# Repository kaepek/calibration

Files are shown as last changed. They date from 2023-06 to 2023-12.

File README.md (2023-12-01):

# KAEPEK-CALIBRATION V1.3.0

A calibration library for synchronising bldc motor voltage models with digital absolute position rotary encoders. Note for now this library is only configured for using the AS5147P encoder with [this breakout circuit](https://www.mouser.co.uk/ProductDetail/ams-OSRAM/AS5147P-TS_EK_AB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)

# Galvanically isolated ADC/Encoder circuit
[Circuit](./circuits/calibration/circuit)

## Connecting AS5147P breakout circuit to the calibration circuit

Connection is made by simply connecting a 8 pin header ribbon cable between the encoder and the calibration circuit. See below:

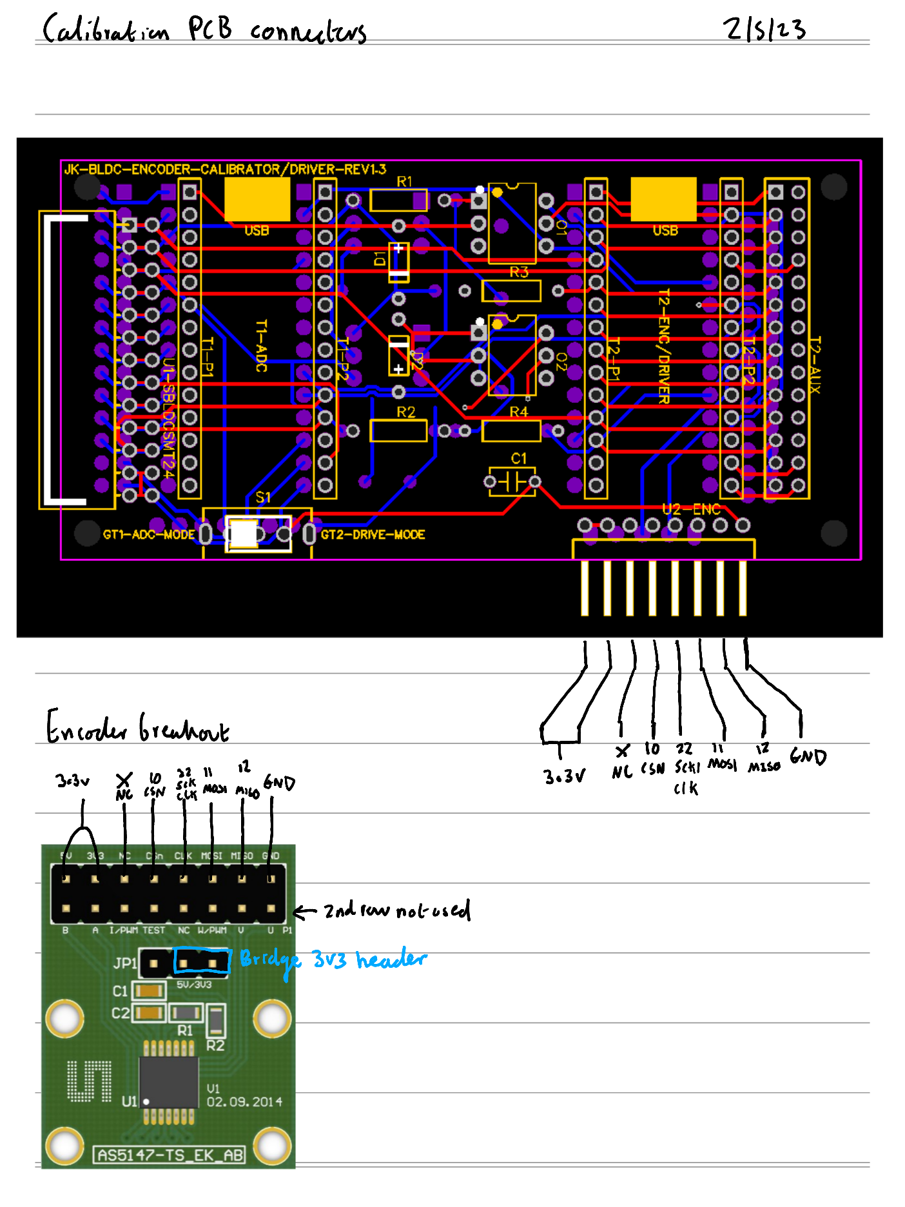
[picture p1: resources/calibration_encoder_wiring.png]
calibration connections


# KAEPEK-SBDLC-SMT-V2.4.0 circuit

[Circuit](https://github.com/kaepek/sbldc-smt/tree/e0ab160f8fc606f709ad24c7c99f17e19a991b6a/circuit)

## Connecting KAEPEK-SBDLC-SMT-V2.4.0 circuit to the calibration circuit

Connection is made by simply connecting the 13 pin header from the KAEPEK-SBDLC-SMT-V2.4.0 pcb to the KAEPEK-Calibration circuit pcb with the surface mount components point upwards. 

# Collecting ADC Encoder data for calibration instructions

## Prerequisites to collection procedure

Need two computers to collect clean data from this setup. The computer must remain isolated from each other not sharing a ground connection (both cannot have ethernet connecting to the same device, stick to WiFi).

- Install node.js (v18.12.1) and npm (8.19.2) have been checked to work.
- Run `npm install` in the projects root directory.
- Install [`kaepek-io`](https://github.com/kaepek/io) as per the README instructions.

## Collection procedure

1. Modify zero_crossing_adc.ino and set the PWM_FREQUENCY to full calibration logging speed e.g. 90kHz.
2. Make sure zero_crossing_adc.ino has been loaded onto the Teensy 4.0 #1.
3. Make sure AS5147P_teensy40.ino has been loaded onto the Teensy 4.0 #2.
4. Find network address of computer #1 and computer #2 by running `ifconfig` or similar. e.g. '192.168.0.15'.
5. Plug Teensy 4.0 #2 (Encoder) into computer #2.
6. Plug Teensy 4.0 #1 (ADC) into computer #1
7. Unplug and replug Teensy 4.0 #1 into computer #1 (forcing a reset).
8. Start the network sync program on computer #1 and provide a name for this data collection run e.g. 'aug_18_test_1'. `npm run network-serial:collect-sync --run_id=aug_18_test_1`. 
9. SSH to computer #2.
10. Start the network source program on computer #2. `npm run network-serial:collect-source --device_id=1 --sync_host=10.0.0.110 --seconds_to_collect=2` .
11. Use a power drill to spin the motor at a constant high angular velocity.
12. Start the network source program on computer #1. `npm run network-serial:collect-source --device_id=0 --sync_host=0.0.0.0 --seconds_to_collect=2` .
13. After you are happy enough data has been collected stop collection by unplugging Teensy 4.0 #1.
14. Ensure `network-serial:collect-source` is stopped for both computers. By typing `Ctrl-c` into the relevant terminal sessions.
15. At this point the `network-serial:collect-sync` will merge the dataset and create an output file `./calibration-data/[run_id].jsonl` on computer #1. If this does not work try manually merging the files, see the next section below, otherwise move on to [data analysis section](#data-analysis).

# Data analysis

Depending on what type of motor controller you are implementing there are different analysis commands you need to run.
The calibration library provides for 3 main types of motor controller:

- 6 step, 3 phase H-Bridge, PWM motor controllers (Trapezoidal Commutation [TC])
- 3 phase H-Bridge, sinusoidal fit (Sinudoidal model fit fom BEMF measurements) PWM motor controllers (Sinusoidal PWM [SPWM])
- 3 phase H-Bridge, direct fit (fit direcly from BEMF measurements) PWM motor controllers (Direct PWM [DPWM])

In either case the raw capture data needs to be combined from the ADC and Encoder microcontroller collected data (for each run) and the result processed to smooth out errors via the [combination and smoothing procedure](#combination-and-smoothing-procedure)

## Prerequisites to performing any Data analysis

- Create a virtual environment: `npm run install:venv`
- Source the virtual environment (must be active before running analysis or for each new terminal session): `source env/bin/activate`
- Install the virtual environment dependancies: `npm run install:venv-deps`

## Combination and smoothing procedure

0. Requires that data has been collected following the [data collection procedure](#collection-procedure)
1. One can run the combination and smoothing process with existing settings (determined by trial and error) using the following command (make sure to check the `kalman_smoothed_merged_capture_data.html` and the `zero_crossing_detections.channels.inliers.html` file! This step is not easily automatable):
  - `npm run combine-and-smooth:rotation-voltage-data -run_id=[run_id]`

Examples of good captures:
  - [Good ADC / Encoder capture with Kalman filtering example output of smooth:rotation-voltage-data for a motor with approximately a sinusoidal bemf motor (A2212)](./dist/kalman_smoothed_merged_capture_data.html)
  - [Good ADC / Encoder with a Kalman filtered example output of smooth:rotation-voltage-data for a motor with a trapazodial bemf motor (Tarot 4006)](./dist/kalman_smoothed_merged_capture_data_tarot4006_sept_12_23_cw_3_trapazodial.html)

Examples of bad captures:
  - [Bad capture example 1- High noise](./dist/kalman_smoothed_merged_capture_data_a2212_jul_26_2s_cw_1_high_noise.html)
  - [Bad capture example 2 - One channel higher](./dist/kalman_smoothed_merged_capture_data_a2212_oct_21_cw_1_higher_channel.html)
  - [Sync loss with one channel also higher](./dist/kalman_smoothed_merged_capture_data_a2212_oct_21_ccw_1_sync_loss.html)
  - [Dead channel](./dist/kalman_smoothed_merged_capture_data_a2212_mar_14_2s_cw_dead_channel.html)

## Fitting procedures:

Then depending on which motor controller you are implementing (TC, SPWM, DPWM) you need to follow the relevant section:

### TC procedure

The TC procdure will map angular segments of the motor to their commutation state. Such that microcontrollers can simply lookup the commutation state based on the angle that the encoder currently sits and therefore apply the correct commutation state as the motor proceeds around the circle. A map is generated for each direction.

The TC procedure require Apache Spark installation v3.5.0 and Spark must be running locally by running the relevant start script e.g. `./spark-3.5.0-bin-hadoop3/sbin/start-all.sh`. Configure the `package.json` spark master url etc.

0. Run the [combination and smoothing procedure](#combination-and-smoothing-procedure)
1. Perform the TC analysis: `npm run perform-tc-analysis --run_id=[run_id] --number_of_poles=[number of poles]`

Then after inspecting the analysis for each run and determining a set of `run_id`s which represent good captures (no artifacts) one can then combine the multiple runs together and obtain the analysis reports and resulting fits for the TC procedure:

2. `npm run combine-datasets:zero-crossing-inliers --run_ids=16sept_ccw,16sept_4_cw`

A html file e.g. `combination-report-lqwkwldkjpvgmrbeqcop.html`, an id file e.g.
`combination-report-lqwkwldkjpvgmrbeqcop.id` and a 6 step fit c++ file `commutation_state_lqwkwldkjpvgmrbeqcop.cpp` will be created in the [calibration-data folder](./calibration-data/), `lqwkwldkjpvgmrbeqcop` represents the identifier for the combined set of analysed run results. Make sure to check for artifacts from the combined report and remove any run_ids where there is bad data.

### SPWM procedure

The SPWM procedure will take the results from the TC/Smoothing procedure and do its best to fit 3 sinusoids to the data (for each phase), for each direction an angular displacement (degrees away from the 0th encoder step) and an angular phase displacement (the phase seperation between the 3 phases) which leads to the least squares error. Thus the motor constants can be used to create a lookup table within the motor controller so that for each direction the controller can apply an appropriate duty for each phase give an input which is the encoder step at any given time.

1. Peform the same instructions as the [TC procedure section](#tc-procedure)
2. Fit a sinusoid model to the data using either of the following commands:
    - Fit a sine wave to the zero crossing data obtained from the TC procedure: `npm run fit-sine:zc --combination_identifier=lqwkwldkjpvgmrbeqcop --number_of_poles=22`
    - Fit a sine wave to the raw zero crossing data obtained from the TC procedure: `npm run fit-sine:raw --combination_identifier=lqwkwldkjpvgmrbeqcop --number_of_poles=22`

Note the `fit-sine:zc` benefits from significant outlier reduction and so in most cases represents the superior method to obtaining the motor constant fits. Depending on the sinusoidal fit method run one can either obtains the motor constants from the following files in the [calibration folder](./calibration-data/), `zc_reconstruction_lqwkwldkjpvgmrbeqcop.png` which is the output of running the `fit-sine:zc` program or `raw_reconstruction_ynitlldoqesyyvgyuwyg.png` which is the ouput of running the `fit-sine:raw` program.

### DPWM procedure

To deal with the inadequacies of the SPWM fitting method arising from the fact that no motors are in fact manufactured perfectly (discrepancies in motor pole strength and inperfect pole spacing) the direct bemf fit method is implemented here. This precedure takes the raw combination data (bemf voltage and angle data) for each run and then superimposes the data (grouped by the encoder angle) and then averages the for each angle the voltage, it applies a normalisation per channel such that one can obtain a single lookup table per direction per phase which informs the motor controller what duty to apply given an input encoder step at any given time. The normalised data can then be loaded into a relevant microcontroller and used the model used to drive the motor forward in a given direction.

This procedure offer the most efficient motor controller model fit of any of the methods proposed here, as the motor phase voltages are played back from direct recordings of the bemf and thus track them quite accurately.

0. Run the [combination and smoothing procedure](#combination-and-smoothing-procedure)
1. Run a direct fit:
    - If you have already run a TC procedure prior to this analysis you may run the following example command: `npm run fit-direct:raw --combination_identifier=lqwkwldkjpvgmrbeqcop`
    - Otherwise you can directly obtain a fit using the following example command: `npm run fit-direct-solo:raw --run_ids=16sept_ccw,16sept_4_cw && npm run graph-direct-solo:raw`, you will obtain an output html, png and c++ file e.g. `combination-direct-fit-ewgtelyqvgfuvropsmif.csv.html`, `raw_reconstruction_direct_comp2_ewgtelyqvgfuvropsmif.png`, `combination-direct-fit-ewgtelyqvgfuvropsmif.cpp`

# Troubleshooting:

- Permission denied when trying to run `network-serial:collect-source`
  - Change permissions for Teensy device `sudo chmod a+rw /dev/ttyACM0`
- One voltage channel 's(A,B,C) peak (in inspect) is larger than the other one.
  - Check circuit connections

# Documentation
Requires running `npm run generate:docs`

- [JS Docs](./docs/global.html)
- Python Docs (TODO)

# 3rd party useful component information:

## H11L1 Opto-isolator

- [Datasheet](https://www.mouser.com/datasheet/2/149/H11L1M-1010369.pdf)

## AS5147P Encoder

- [Datasheet](https://ams.com/documents/20143/36005/AS5147P_DS000328_2-00.pdf)

# How to prepare the Teensy40 platform:
- Install [Arduino IDE v1.8.19](https://www.arduino.cc/en/software)
- Install [Teensyduino v2.1.0](https://www.pjrc.com/teensy/teensyduino.html)

# General dependancies:

- [Arduino.h](https://github.com/arduino/ArduinoCore-avr)
- [imxrt.h](https://github.com/PaulStoffregen/cores/tree/master)
- [Serialport](https://github.com/serialport/node-serialport/blob/main/LICENSE)
- [Bokeh](https://github.com/bokeh/bokeh/blob/branch-3.4/LICENSE.txt)
- [Typed struct](https://github.com/sarakusha/typed-struct/blob/main/LICENSE)
- [Extensionless](https://github.com/barhun/extensionless/blob/main/LICENSE)
- [Cross var](https://github.com/elijahmanor/cross-var/blob/master/LICENSE)
- [JS promise socket](https://github.com/dex4er/js-promise-socket)
- [JS Doc](https://github.com/jsdoc/jsdoc/blob/main/LICENSE)
- [Numpy](https://github.com/numpy/numpy/blob/main/LICENSE.txt)
- [Pandas](https://github.com/pandas-dev/pandas)
- [Spark](https://github.com/apache/spark/blob/master/LICENSE)
- [netifaces](https://alastairs-place.net/projects/netifaces/)
- [pyarrow](https://github.com/apache/arrow/blob/main/LICENSE.txt)
- [scipy](https://github.com/scipy/scipy)
- [colour](https://github.com/vaab/colour/blob/master/LICENSE)
- [matplotlib](https://github.com/matplotlib/matplotlib)

## [See the long version of this article](./README-LONG.md)

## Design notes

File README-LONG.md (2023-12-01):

# KAEPEK-CALIBRATION V1.3.0

A calibration library for synchronising bldc motor voltage models with digital absolute position rotary encoders. Note for now this library is only configured for using the AS5147P encoder with [this breakout circuit](https://www.mouser.co.uk/ProductDetail/ams-OSRAM/AS5147P-TS_EK_AB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)

# Quickstart Guide

Recommended [read the quick start guide here](./README.md).
For more comprehensive instructions continue below.

# Galvanically isolated ADC/Encoder circuit

[Circuit](./circuits/calibration/circuit)

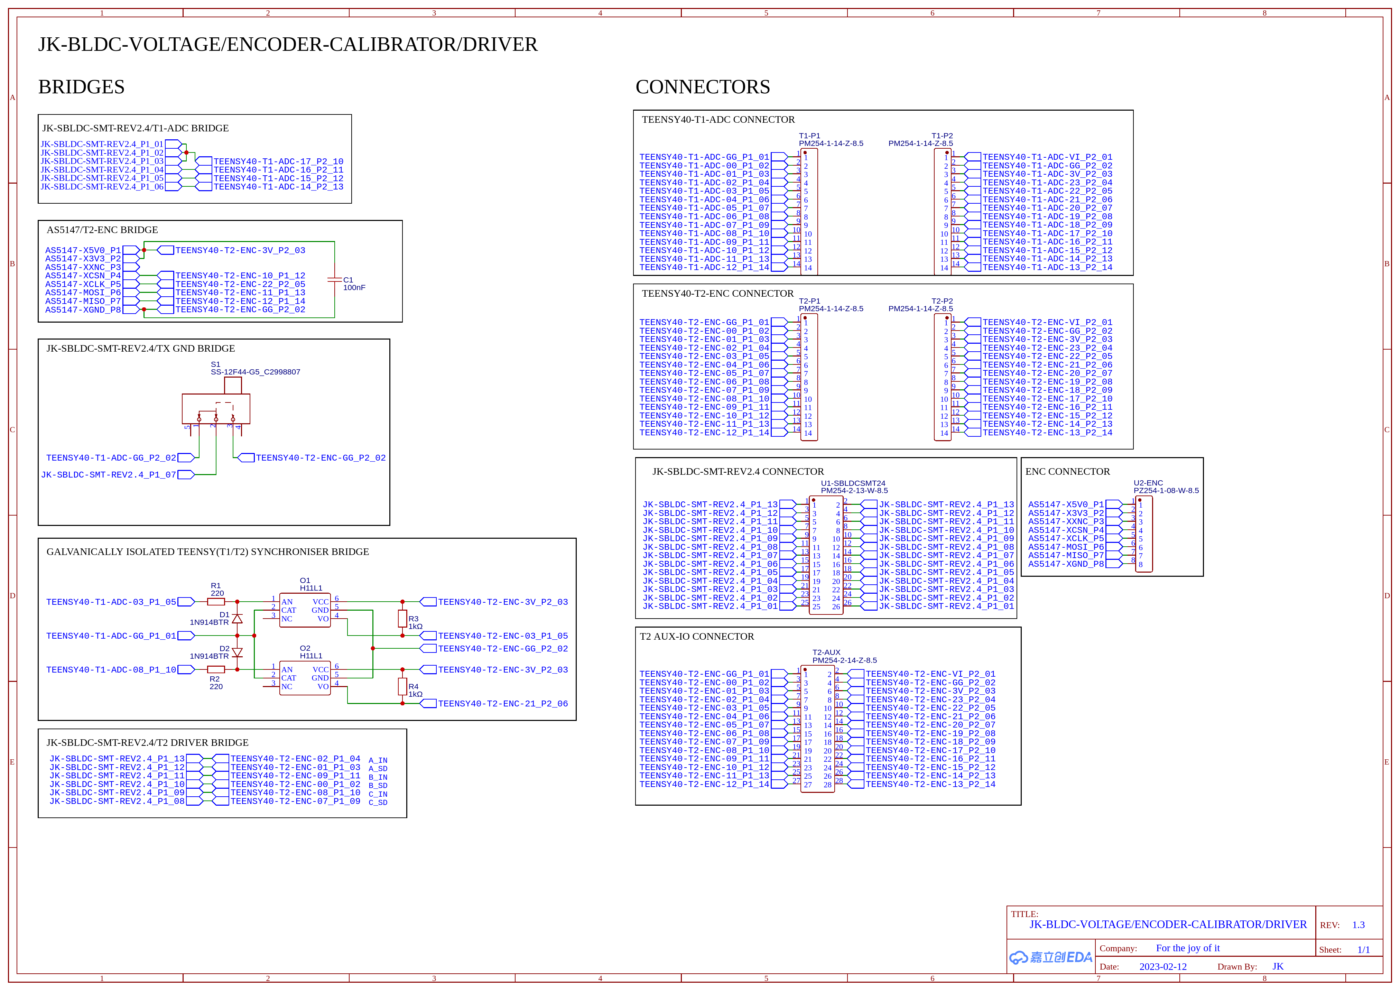
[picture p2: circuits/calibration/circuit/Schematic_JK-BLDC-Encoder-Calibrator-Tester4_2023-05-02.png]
calibration circuit


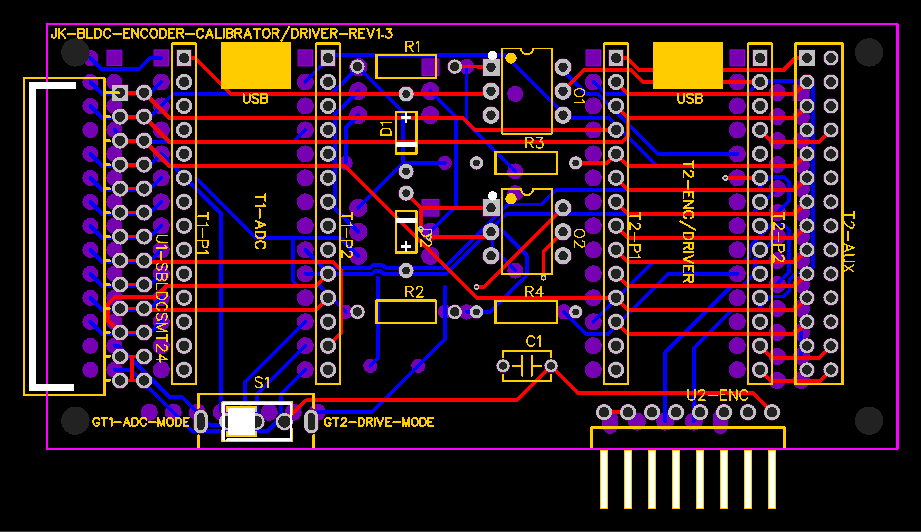
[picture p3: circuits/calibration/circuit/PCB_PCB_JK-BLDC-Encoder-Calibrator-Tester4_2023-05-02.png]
calibration pcb


## Connecting AS5147P breakout circuit to the calibration circuit

Connection is made by simply connecting a 8 pin header ribbon cable between the encoder and the calibration circuit. See below:

calibration connections

Specific pin connections are mentioned below for reference:

### Encoder information table

AS5147 pin| 5v| 3.3v| x| csn| clk| mosi| miso| GND
:-----:|:-----:|:-----:|:-----:|:-----:|:-----:|:-----:|:-----:|:-----:
Teensy 4.0 #2 pin| 3.3v| 3.3v| x| 10| 22| 11| 12| GND

### Connecting Teensy 4.0 #1 with Teensy 4.0 #2 with two H11L1 optocouplers

Teensy 4.0 #1 acts as a master and sends signals via two galvanically isolated optocouplers to Teensy 4.0 #2. 

### Connection information table

H11L1 #1 RESET pin| 1 (ANODE)| 2 (CATHODE)| 3(NC)| 4(Vo)| 5 (GND)| 6(VCC)
:-----:|:-----:|:-----:|:-----:|:-----:|:-----:|:-----:
Teensy 4.0 #1 pin| 3| GND| X| X| X| X
Teensy 4.0 #2 pin| X| X| X| 3| GND| 3.3V

H11L1 #2 CLK pin| 1 (ANODE)| 2 (CATHODE)| 3(NC)| 4(Vo)| 5 (GND)| 6(VCC)
:-----:|:-----:|:-----:|:-----:|:-----:|:-----:|:-----:
Teensy 4.0 #1 pin| 8| GND| X| X| X| X
Teensy 4.0 #2 pin| X| X| X| 21| GND| 3.3V

# SBLDC-SMT circuit

[Circuit](https://github.com/kaepek/sbldc-smt/tree/e0ab160f8fc606f709ad24c7c99f17e19a991b6a/circuit)

Note that one the voltage divider grid is used for this use case which enables reading voltages from phase A,B,C and the common virtual neutral (VN).

sbldc-smt circuit

sbldc-smt pcb

## Connecting KAEPEK-SBDLC-SMT-V2.4.0 circuit to the calibration circuit

Connection is made by simply connecting the 13 pin header from the KAEPEK-SBDLC-SMT-V2.4.0 pcb to the KAEPEK-Calibration circuit pcb with the surface mount components point upwards. 

Specific pin connections are mentioned below for reference:

### ADC/ADC-ETC information table

| PHASE | A | B | VN | C |
|---|-----|---|---|---|
| Teensy 4.0 #1 pin | 14  | 15 | 17 | 16 |
| COLOUR | RED | YELLOW | GREEN | BLACK |
| TRIG | 0 | 1 | 2 | 3 |
| DONE | 0 | 1 | 0 | 1 |
| HW-CH | 1 | 2 | 3 | 4 |
| ADC-CH | 7 | 8 | 11 | 12 |

### Other pins

- Connect Teensy 4.0 #1 ground to pin 7 of KAEPEK-SBDLC-SMT#V2.4.0

# Collecting ADC Encoder data for calibration instructions

## Prerequisites to collection procedure

Need two computers to collect clean data from this setup. The computer must remain isolated from each other not sharing a ground connection (both cannot have ethernet connecting to the same device, stick to WiFi).

- Install node.js (v18.12.1) and npm (8.19.2) have been checked to work.
- Run `npm install` in the projects root directory.
- Install [`kaepek-io`](https://github.com/kaepek/io) as per the README instructions.

## Collection procedure

1. Modify zero_crossing_adc.ino and set the PWM_FREQUENCY to full calibration logging speed e.g. 90kHz.
2. Make sure zero_crossing_adc.ino has been loaded onto the Teensy 4.0 #1.
3. Make sure AS5147P_teensy40.ino has been loaded onto the Teensy 4.0 #2.
4. Find network address of computer #1 and computer #2 by running `ifconfig` or similar. e.g. '192.168.0.15'.
5. Plug Teensy 4.0 #2 (Encoder) into computer #2.
6. Plug Teensy 4.0 #1 (ADC) into computer #1
7. Unplug and replug Teensy 4.0 #1 into computer #1 (forcing a reset).
8. Start the network sync program on computer #1 and provide a name for this data collection run e.g. 'aug_18_test_1'. `npm run network-serial:collect-sync --run_id=aug_18_test_1`. 
9. SSH to computer #2.
10. Start the network source program on computer #2. `npm run network-serial:collect-source --device_id=1 --sync_host=10.0.0.110 --seconds_to_collect=2` .
11. Use a power drill to spin the motor at a constant high angular velocity.
12. Start the network source program on computer #1. `npm run network-serial:collect-source --device_id=0 --sync_host=0.0.0.0 --seconds_to_collect=2` .
13. After you are happy enough data has been collected stop collection by unplugging Teensy 4.0 #1.
14. Ensure `network-serial:collect-source` is stopped for both computers. By typing `Ctrl-c` into the relevant terminal sessions.
15. At this point the `network-serial:collect-sync` will merge the dataset and create an output file `./calibration-data/[run_id].jsonl` on computer #1. If this does not work try manually merging the files, see the next section below, otherwise move on to [data analysis section](#data-analysis).

## Manually merging the datasets if network merge fails

1. Each source program will write to the `/tmp` folder before network transmission is attempted. Take the `/tmp/serial-data-device-[x].jsonl` file from the `/tmp` folder's from each computer and place into a folder under `./calibration-data/[experiment-name]/` of computer #1.
2. Combine datasets into a single file `node calibration/combine-multicapture-files.js [experiment-name]`
3. Rename the resultant file the same name as the experiment name `[experiment-name].jsonl` and move to parent folder.
4. Combine the collected `[experiment-name].jsonl` `npm run combine:rotation-voltage-network-data --dataset=[experiment-name].jsonl`, you will recieve a file `[experiment-name].jsonl.matched.csv` if the successful, this program will report how successful it was in matching records high match rate is expect ~98%.
5. Proceed from step 1 from the analysis instructions.

This collection process must be performed for a number of experimental runs for each direction `clockwise` and `counter-clockwise`, I would recommend performing multiple runs in each direction, say atleast 3 in each direction. When performing the [data analysis section](#data-analysis) on each run you may find that some of the runs encountered issues and have artifacts in the collected data, in this case I would recommend repeating the collection process with a set of new experiments to replace the bad captures with good ones.

# Data analysis

Depending on what type of motor controller you are implementing there are different analysis commands you need to run.
The calibration library provides for 3 main types of motor controller:

- 6 step, 3 phase H-Bridge, PWM motor controllers (Trapezoidal Commutation [TC])
- 3 phase H-Bridge, sinusoidal fit (Sinudoidal model fit fom BEMF measurements) PWM motor controllers (Sinusoidal PWM [SPWM])
- 3 phase H-Bridge, direct fit (fit direcly from BEMF measurements) PWM motor controllers (Direct PWM [DPWM])

In either case the raw capture data needs to be combined from the ADC and Encoder microcontroller collected data (for each run) and the result processed to smooth out errors via the [combination and smoothing procedure](#combination-and-smoothing-procedure)

## Prerequisites to performing any Data analysis

- Create a virtual environment: `npm run install:venv`
- Source the virtual environment (must be active before running analysis or for each new terminal session): `source env/bin/activate`
- Install the virtual environment dependancies: `npm run install:venv-deps`

## Combination and smoothing procedure

0. Requires that data has been collected following the [data collection procedure](#collection-procedure)
1. Combine the collected `./calibration-data/[run_id]/raw_capture_data.jsonl` file `npm run combine:rotation-voltage-network-data --run_id=[run_id]`, you will recieve a file `merged_capture_data.csv` in the `./calibration-data/[run_id]` folder if successful, this program will report how well it matched records, high match rate is expect ~98% for good runs. Less than 98% can indicate a loss of sync between the ADC and Encoder microcontroller data recorders, or other issues, try re-running a new trial experiment in this case and abandon the bad data capture.
2. Inspect the `./calibration-data/[run_id]/merged_capture_data.csv` file using the following command and tune the kalman settings at the top of the relevant file `tune-rotation-voltage-data-smoothing.py` (trial and error if nessesary, looking for kalman closely following the signal without to much noise).
    - `npm run inspect:rotation-voltage-data --run_id=[run_id]`
3. When you are happy with the quality of the kalman tuning, you can now commit to smooth the data and save it using the command following (make sure to apply the good Kalman constants from the `tune-rotation-voltage-data-smoothing.py` file to the top of the `smooth-rotation-voltage-data.py` file). This will create a `kalman_smoothed_merged_capture_data.json` file within `./calibration-data/[run_id]` folder, as well as a html report file `kalman_smoothed_merged_capture_data.html`.
    - `npm run smooth:rotation-voltage-data --run_id=[run_id]`
4. Make sure to process inspect the resulting `kalman_smoothed_merged_capture_data.html` file to manually check that there are no artifacts. There are many types of possible artifacts, one channel being higher or lower than the other two channels (indicating a problem with the motor connectors), excessive noise in the data collection (many possible reasons for this, try again), and a loss of sync between the ADC and the Encoder recordings, observable discontinuity in the encoder saw tooth pattern (bad luck! try again).

Examples of good captures:
  - [Good ADC / Encoder capture with Kalman filtering example output of smooth:rotation-voltage-data for a motor with approximately a sinusoidal bemf motor (A2212)](./dist/kalman_smoothed_merged_capture_data.html)
  - [Good ADC / Encoder with a Kalman filtered example output of smooth:rotation-voltage-data for a motor with a trapazodial bemf motor (Tarot 4006)](./dist/kalman_smoothed_merged_capture_data_tarot4006_sept_12_23_cw_3_trapazodial.html)

Examples of bad captures:
  - [Bad capture example 1- High noise](./dist/kalman_smoothed_merged_capture_data_a2212_jul_26_2s_cw_1_high_noise.html)
  - [Bad capture example 2 - One channel higher](./dist/kalman_smoothed_merged_capture_data_a2212_oct_21_cw_1_higher_channel.html)
  - [Sync loss with one channel also higher](./dist/kalman_smoothed_merged_capture_data_a2212_oct_21_ccw_1_sync_loss.html)
  - [Dead channel](./dist/kalman_smoothed_merged_capture_data_a2212_mar_14_2s_cw_dead_channel.html)

For convenience one can run the combination and smoothing process with existing settings (determined by trial and error) using the following command (make sure to check the `kalman_smoothed_merged_capture_data.html` file! This step is not easily automatable):

- `npm run combine-and-smooth:rotation-voltage-data -run_id=[run_id]`

## Fitting procedures:

Then depending on which motor controller you are implementing (TC, SPWM, DPWM) you need to follow the relevant section:

### TC procedure

The TC procdure will map angular segments of the motor to their commutation state. Such that microcontrollers can simply lookup the commutation state based on the angle that the encoder currently sits and therefore apply the correct commutation state as the motor proceeds around the circle. A map is generated for each direction.

The TC procedure require Apache Spark installation v3.5.0 and Spark must be running locally by running the relevant start script e.g. `./spark-3.5.0-bin-hadoop3/sbin/start-all.sh`. Configure the `package.json` spark master url etc.

0. Run the [combination and smoothing procedure](#combination-and-smoothing-procedure)
1. With data now smoothed to minimise zero-crossing detection errors you can apply zero-crossing detection. This will create a `zero_crossing_detections.channels.all.json` which contains grouped lists of angles for each channel cluster e.g. 'zc_channel_af_data' which stands for zero crossing channel phase A falling, where a given phaseA-vn crossed zero. Also a `zero_crossing_detections.histogram.all.json` file will be created which contains any zero crossing events for each channel organised by angle.
  - `npm run detect:zero-crossing --run_id=[run_id]`
2. Now for each channel we should have `motor_poles/2` zero-crossing events, noise will prevent us knowing the exact angle where this happenes, we will in fact have a distribtion of points clustered around `motor_poles/2` centers... thus we can cluster the zero-crossing events into `motor_poles/2` groups. This will create a `kmedoids_clustered_zero_crossing_channel_detections.all.json` files, containing the clustered angles and their centroids (mean points) for each channel.
  - `npm run cluster:zero-crossing --run_id=sept2 --number_of_poles=14`.
3. Next we need to analyse how well the clustering went. Important metrics will be the mean point of each cluster, the standard deviation of each cluster and finally we need a map which identifes for each angle which channel cluster represents that point best if any. The following file is created showing this data `kmedoids_clustered_zero_crossing_channel_detections.all.analysis.json`.
  - `npm run analyse:zero-crossing-channel-clusters --run_id=sept2`
4. Next we need to see the results of the analysis, also we need to use the statistics generated to eliminate cluster outliers a program is provided to do this. A file `zero_crossing_detections.channels.outliers.json` is produced which contains the outliers detected for each channel, a file `zero_crossing_detections.channels.inliers.json` is produces which contain valid inliers per channel and finally a report file `zero_crossing_detections.channels.all.html` is generated to visualise this analysis.
  - `npm run inspect:zero-crossing --run_id=sept2`
5. Next with the outliers removed from the dataset and stored in their own file `zero_crossing_detections.channels.inliers.json`, we need to re-cluster the channels into `motor_poles/2` groups again to create a new file `kmedoids_clustered_zero_crossing_channel_detections.inliers.json`.
  - `npm run cluster-inliers:zero-crossing --run_id=sept2 --number_of_poles=14`
6. Next we need to re-analyse the re-clustered channel zero-crossing angles to create a new analysis file `kmedoids_clustered_zero_crossing_channel_detections.inliers.analysis.json`.
  - `npm run analyse-inliers:zero-crossing-channel-clusters --run_id=sept2`
7. Next we need to see the results of the re-analysis post outlier elimination.
  - `npm run inspect-inliers:zero-crossing --run_id=sept2`

For convenience one can run a single command to perform all off these steps (including the combination and smoothing procedure) for a given `run_id` using the following command:

1. `npm run perform-tc-analysis --run_id=[run_id] --number_of_poles=[number of poles]`

Then after inspecting the analysis for each run and determining a set of `run_id`s which represent good captures (no artifacts) one can then combine the multiple runs together and obtain the analysis reports and resulting fits for the TC procedure:

2. `npm run combine-datasets:zero-crossing-inliers --run_ids=16sept_ccw,16sept_4_cw`

A html file e.g. `combination-report-lqwkwldkjpvgmrbeqcop.html`, an id file e.g.
`combination-report-lqwkwldkjpvgmrbeqcop.id` and a 6 step fit c++ file `commutation_state_lqwkwldkjpvgmrbeqcop.cpp` will be created in the [calibration-data folder](./calibration-data/), `lqwkwldkjpvgmrbeqcop` represents the identifier for the combined set of analysed run results.

### SPWM procedure

The SPWM procedure will take the results from the TC/Smoothing procedure and do its best to fit 3 sinusoids to the data (for each phase), for each direction an angular displacement (degrees away from the 0th encoder step) and an angular phase displacement (the phase seperation between the 3 phases) which leads to the least squares error. Thus the motor constants can be used to create a lookup table within the motor controller so that for each direction the controller can apply an appropriate duty for each phase give an input which is the encoder step at any given time.

1. Peform the same instructions as the [TC procedure section](#tc-procedure)
2. Fit a sinusoid model to the data using either of the following commands:
    - Fit a sine wave to the zero crossing data obtained from the TC procedure: `npm run fit-sine:zc --combination_identifier=lqwkwldkjpvgmrbeqcop --number_of_poles=22`
    - Fit a sine wave to the raw zero crossing data obtained from the TC procedure: `npm run fit-sine:raw --combination_identifier=lqwkwldkjpvgmrbeqcop --number_of_poles=22`

Note the `fit-sine:zc` benefits from significant outlier reduction and so in most cases represents the superior method to obtaining the motor constant fits. Depending on the sinusoidal fit method run one can either obtains the motor constants from the following files in the [calibration folder](./calibration-data/), `zc_reconstruction_lqwkwldkjpvgmrbeqcop.png` which is the output of running the `fit-sine:zc` program or `raw_reconstruction_ynitlldoqesyyvgyuwyg.png` which is the ouput of running the `fit-sine:raw` program.

#### TODO CHECK FILE NAMES

The motor constants and their errors can be obtained in the title of the graph, you can inspect the graphs (the source data and the fit) and compare their extrema to gain some intuition as to the validity of the fit.

Note these methods do assume that the motors are periodically consistant, which is often not the case in reality.

### DPWM procedure

To deal with the inadequacies of the SPWM fitting method arising from the fact that no motors are in fact manufactured perfectly (discrepancies in motor pole strength and inperfect pole spacing) the direct bemf fit method is implemented here. This precedure takes the raw combination data (bemf voltage and angle data) for each run and then superimposes the data (grouped by the encoder angle) and then averages the for each angle the voltage, it applies a normalisation per channel such that one can obtain a single lookup table per direction per phase which informs the motor controller what duty to apply given an input encoder step at any given time. The normalised data can then be loaded into a relevant microcontroller and used the model used to drive the motor forward in a given direction.

This procedure offer the most efficient motor controller model fit of any of the methods proposed here, as the motor phase voltages are played back from direct recordings of the bemf and thus track them quite accurately.

0. Run the [combination and smoothing procedure](#combination-and-smoothing-procedure)
1. Run a direct fit:
    - If you have already run a TC procedure prior to this analysis you may run the following example command: `npm run fit-direct:raw --combination_identifier=lqwkwldkjpvgmrbeqcop`
    - Otherwise you can directly obtain a fit using the following example command: `npm run fit-direct-solo:raw --run_ids=16sept_ccw,16sept_4_cw && npm run graph-direct-solo:raw`, you will obtain an output html, png and c++ file e.g. `combination-direct-fit-ewgtelyqvgfuvropsmif.csv.html`, `raw_reconstruction_direct_comp2_ewgtelyqvgfuvropsmif.png`, `combination-direct-fit-ewgtelyqvgfuvropsmif.cpp`

# Troubleshooting:

- Permission denied when trying to run `network-serial:collect-source`
  - Change permissions for Teensy device `sudo chmod a+rw /dev/ttyACM0`
- One voltage channel 's(A,B,C) peak (in inspect) is larger than the other one.
  - Check circuit connections

# Documentation
Requires running `npm run generate:docs`

- [JS Docs](./docs/global.html)
- Python Docs (TODO)

# 3rd party useful component information:

## H11L1 Opto-isolator

- [Datasheet](https://www.mouser.com/datasheet/2/149/H11L1M-1010369.pdf)

## AS5147P Encoder

- [Datasheet](https://ams.com/documents/20143/36005/AS5147P_DS000328_2-00.pdf)

# Todos:

- Check file names
- Upload examples of bad / good plots
- Re-test everything watch out where i have renamed files outputs
- add disclaimer as to quality

# How to prepare the Teensy40 platform:
- Install [Arduino IDE v1.8.19](https://www.arduino.cc/en/software)
- Install [Teensyduino v2.1.0](https://www.pjrc.com/teensy/teensyduino.html)

# General dependancies:

- [Arduino.h](https://github.com/arduino/ArduinoCore-avr)
- [imxrt.h](https://github.com/PaulStoffregen/cores/tree/master)
- [Serialport](https://github.com/serialport/node-serialport/blob/main/LICENSE)
- [Bokeh](https://github.com/bokeh/bokeh/blob/branch-3.4/LICENSE.txt)
- [Typed struct](https://github.com/sarakusha/typed-struct/blob/main/LICENSE)
- [Extensionless](https://github.com/barhun/extensionless/blob/main/LICENSE)
- [Cross var](https://github.com/elijahmanor/cross-var/blob/master/LICENSE)
- [JS promise socket](https://github.com/dex4er/js-promise-socket)
- [JS Doc](https://github.com/jsdoc/jsdoc/blob/main/LICENSE)
- [Numpy](https://github.com/numpy/numpy/blob/main/LICENSE.txt)
- [Pandas](https://github.com/pandas-dev/pandas)
- [Spark](https://github.com/apache/spark/blob/master/LICENSE)
- [netifaces](https://alastairs-place.net/projects/netifaces/)
- [pyarrow](https://github.com/apache/arrow/blob/main/LICENSE.txt)
- [scipy](https://github.com/scipy/scipy)
- [colour](https://github.com/vaab/colour/blob/master/LICENSE)
- [matplotlib](https://github.com/matplotlib/matplotlib)

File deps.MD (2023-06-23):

analysis-zc-reconstruct.py 
analysis-raw-reconstruct.py 

network-multicapture-combine.py => pandas
smooth-rotation-voltage-data.py => numpy, kalman, bokeh
tune-rotation-voltage-data-smoothing.py => numpy, bokeh, kalman
zero-cross-spark.py => pyspark, spark_context, pandas
zero-cross-cluster-data.py => pyspark, numpy, spark_context, kmedoids2, metrics
analyse-zero-cross-cluster-data.py => bokeh, metrics, analyse
zero-cross-inspect.py => bokeh, numpy, metrics, analyse
zero-cross-inspect-inliers.py => bokeh, numpy, metrics, report, analyse

network-multicapture-sync.js => serialport, promisesocket
network-multicapture-source.js 

combine-rotation-datasets-cw-and-ccw.py => numpy, kmedoids, analyse

numpy==1.24.1
pandas==1.4.2
pyspark==3.2.1

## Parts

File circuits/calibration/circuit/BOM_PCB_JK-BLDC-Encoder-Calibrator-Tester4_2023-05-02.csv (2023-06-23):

ID | Name | Designator | Footprint | Quantity | Manufacturer Part | Manufacturer | Supplier | Supplier Part | Price | Pins | 3DModel | Contributor | Resistance | link
1 | 100nF | C1 | CAP-TH_L5.0-W2.5-P5.08-D0.7 | 1 | CC2A104ZC1ID3F7C30MF | Dersonic(德尔创) | LCSC | C254109 | 0.004 | 2 | CAP-TH_L5.0-W2.5-P5.08 | LCSC |  | https://so.szlcsc.com/global.html?c=&k=C254108
2 | 1N914BTR | D1,D2 | DO-35_BD2.0-L4.2-P8.20-D0.5-RD | 2 | 1N914BTR | onsemi(安森美) | LCSC | C258180 | 0.004 | 2 | DO-35_D1.9-L3.9-P8.2 | LCSC |  | https://item.szlcsc.com/86229.html
3 | H11L1 | O1,O2 | DIP-6_L8.5-W6.4-P2.54-LS7.6-BL | 2 | H11L1 | EVERLIGHT(亿光) | LCSC | C78588 | 0.057 | 6 | DIP-6_L8.7-W6.4-H3.3-LS7.62-P2.54 | lcsc |  | https://item.szlcsc.com/195665.html
4 | 220 | R1,R2 | RES-TH_BD2.4-L6.3-P10.30-D0.6 | 2 | MFR-25FTE52-220R | YAGEO(国巨) | LCSC | C172985 | 0.002 | 2 | RES-TH_BD2.4-L6.3-P10.30-D0.6 | LCSC | 220Ω | https://item.szlcsc.com/184395.html
5 | 1kΩ | R3,R4 | RES-TH_BD2.3-L6.5-P10.50-D0.5 | 2 | MF1/4W-1KΩ±1%T52 | Huaxing Mechanical-Elec. | LCSC | C713997 | 0.001 | 2 | RES-TH_D2.3-L6.5-P10.50 | LCSC | 1kΩ | https://item.szlcsc.com/123457.html
6 | SS-12F44-G5_C2998807 | S1 | SW-TH_SS-12F44-G5_C2998807 | 1 | SS-12F44-G5 | DEALON(德艺隆) | LCSC | C2998807 | 0.006 | 5 | SW-TH_SS-12F44-G5_C2998807 | lcsc |  | https://atta.szlcsc.com/upload/public/pdf/source/20220428/590A0165C728230C4E39516860AD3726.pdf
7 | PM254-1-14-Z-8.5 | T1-P1,T1-P2,T2-P1,T2-P2 | HDR-TH_14P-P2.54-V-F-1 | 4 | PM254-1-14-Z-8.5 | HCTL(华灿天禄) | LCSC | C2897377 | 0.036 | 14 | HDR-TH_14P-P2.54-F-LI-1X14P | LCSC |  | https://item.szlcsc.com/53725.html
8 | PM254-2-14-Z-8.5 | T2-AUX | HDR-TH_28P-P2.54-V-F-R2-C14-S2.54-1 | 1 | PM254-2-14-Z-8.5 | HCTL(华灿天禄) | LCSC | C2897415 | 0.064 | 28 | HDR-TH_28P-P2.54-F-LI-2X14P | LCSC |  | https://item.szlcsc.com/61427.html
9 | PM254-2-13-W-8.5 | U1-SBLDCSMT24 | HDR-TH_26P-P2.54-H-F-R2-C13-W8.5 | 1 | PM254-2-13-W-8.5 | HCTL(华灿天禄) | LCSC | C2897433 | 0.071 | 26 | HDR-TH_26P-P2.54-H-F-R2-C13-W8.5 | LCSC |  | https://atta.szlcsc.com/upload/public/pdf/source/20211012/642A10508B34AD7BE7B9895A6BFCAF0F.pdf
10 | PZ254-1-08-W-8.5 | U2-ENC | HDR-TH_08P-P2.54-H-M-W10.4-N | 1 | PZ254-1-08-W-8.5 | HCTL(华灿天禄) | LCSC | C2894950 | 0.014 | 8 | HDR-TH_08P-P2.54-H-M-W10.4-N | LCSC |  | https://atta.szlcsc.com/upload/public/pdf/source/20210915/B8B8CB82ADCC8CEA5EF9FDE626EB2FA9.pdf

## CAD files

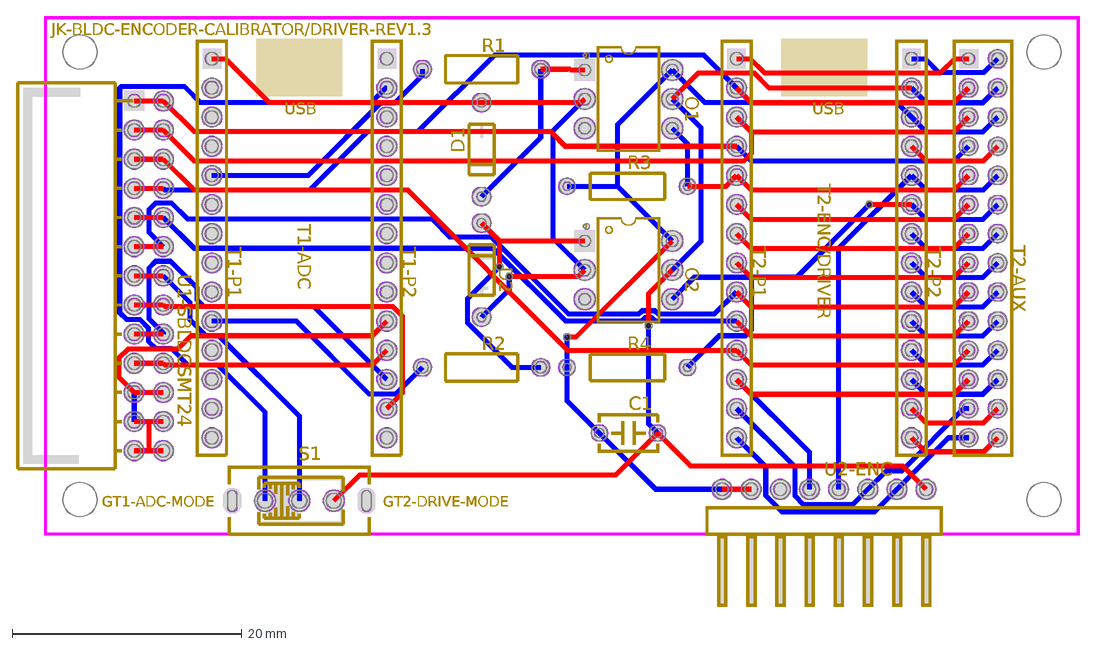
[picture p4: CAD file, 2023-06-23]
circuits/calibration/circuit/PCB_JK-BLDC-Encoder-Calibrator-Tester4_2023-05-02.dxf
JK-BLDC-ENCODER-CALIBRATOR/DRIVER-REV1.3
GT1-ADC-MODE
GT2-DRIVE-MODE
T1-ADC
T2-ENC/DRIVER
USB
C1
D1
D2
O1
O2
R1
R2
R3
R4
S1
T1-P1
T1-P2
T2-P1
T2-P2
T2-AUX
U1-SBLDCSMT24
U2-ENC

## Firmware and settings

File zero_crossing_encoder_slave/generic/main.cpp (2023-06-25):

#include <Arduino.h>
#include <imxrt.h>
#include "log.cpp"
#include "teensy40-AS5147P-rotary-encoder/generic/digital_rotary_encoder.hpp"
#define PIN_TEENSY_SLAVE_RESET 3
#define PIN_TEENSY_SLAVE_CLK 21

volatile uint32_t TIME_CTR = 0;
volatile int DEBOUNCE_DISTANCE_RESET = 1;
elapsedMicros delta_time;
kaepek::DigitalRotaryEncoderSPI encoder;

void MASTER_RESET_FALLING() {
  // debounce
  bool last_state = false;
  for (int i = 0; i < DEBOUNCE_DISTANCE_RESET; i++) {
    bool state = digitalReadFast(PIN_TEENSY_SLAVE_RESET);
    if (state != LOW) {
      return;
    }
  }
  TIME_CTR = 0;
  delta_time = 0;
}

int DEBOUNCE_DISTANCE_CLK = 0;

void MASTER_CLK_FALLING() {
  // without debounce this is probably noisy! 
  // it does loose sync, but probability increased with more capture time, keep capture time below 3 seconds
  cli(); // suppress master reset and master clock, code must complete in time or else sync issues! TESTME
  // inc time
  TIME_CTR++;
  // take encoder reading
  uint16_t value = encoder.read(); // as5147p_get_sensor_value_fast(); old
  // log results to host
  log_encoder_ascii(TIME_CTR, value, delta_time);
  // allow interrupts again TESTME
  sei(); 
}

void slave_input_setup(kaepek::DigitalRotaryEncoderSPI _encoder) {
  pinMode(PIN_TEENSY_SLAVE_CLK, INPUT);
  pinMode(PIN_TEENSY_SLAVE_RESET, INPUT);

  // set encoder reference
  encoder = _encoder;
  encoder.setup();

  attachInterrupt(digitalPinToInterrupt(PIN_TEENSY_SLAVE_RESET), MASTER_RESET_FALLING, FALLING);
  attachInterrupt(digitalPinToInterrupt(PIN_TEENSY_SLAVE_CLK), MASTER_CLK_FALLING, FALLING);
}

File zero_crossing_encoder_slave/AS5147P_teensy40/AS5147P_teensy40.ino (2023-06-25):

#include "generic/teensy40-AS5147P-rotary-encoder/digital_rotary_encoder.cpp"
#include "generic/main.cpp"

kaepek::DigitalEncoderPinsSPI enc_pins = kaepek::DigitalEncoderPinsSPI();
kaepek::DigitalRotaryEncoderSPI enc;

void setup()
{
  // setup encoder
  enc_pins.csn = 10;
  enc_pins.miso = 12;
  enc_pins.mosi = 11;
  enc_pins.sck = 22;
  enc = kaepek::DigitalRotaryEncoderSPI(enc_pins);
  // setup slave and pass enc reference to slave logic which will init the device "setup"
  slave_input_setup(enc);
}

void loop()
{

}

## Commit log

2023-06-23 Release from private repo
    [BOM_PCB_JK-BLDC-Encoder-Calibrator-Tester4_2023-05-02.csv, PCB_JK-BLDC-Encoder-Calibrator-Tester4_2023-05-02.dxf, PCB_JK-BLDC-Encoder-Calibrator-Tester4_2023-0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]
2023-06-25 updating encoder lib
2023-09-26 working on cpp codegen for voltage map
2023-09-28 working new direct voltage map generator
